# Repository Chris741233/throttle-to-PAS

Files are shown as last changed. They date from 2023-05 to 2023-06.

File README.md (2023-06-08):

# e-bike throttle to PAS converter
Arduino e-bike throttle to PAS simulation and replication \
Using a throttle (thumb throttle or accelerator) to simulate pedaling on an e-bike

Utilisation d'un throttle (gachette de pouce ou accélérateur) pour simuler un pédalage sur un e-bike.
  
Code pour Aduino Nano/Uno (signal +5V)

**see also** 
- [Button to PAS (with cruise in option)](https://github.com/Chris741233/button-to-PAS)
- [PAS to throttle converter](https://github.com/Chris741233/PAS_to_throttle)
- [PAS analyzer](https://github.com/Chris741233/PAS_analyzer)

**Discussion sur le forum Cyclurba**  
[Cyclurba](https://cyclurba.fr/forum/forum_discussion.php?from=11&discussionID=31032&messageID=741856&rubriqueID=87)  
[video de Peter (Youtube)](https://www.youtube.com/watch?v=A_oQwdZdAz4&t=2s)

---

#### Wiring (Arduino Uno/Nano)
<p align="left">
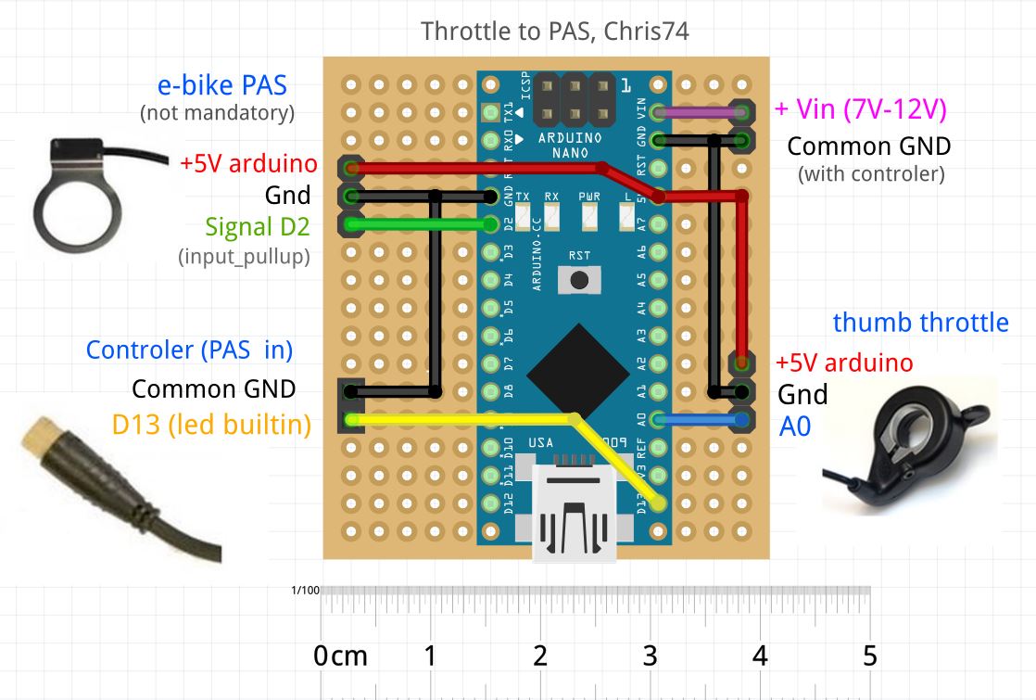
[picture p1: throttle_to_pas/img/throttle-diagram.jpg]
  
</p>

<p align="left">
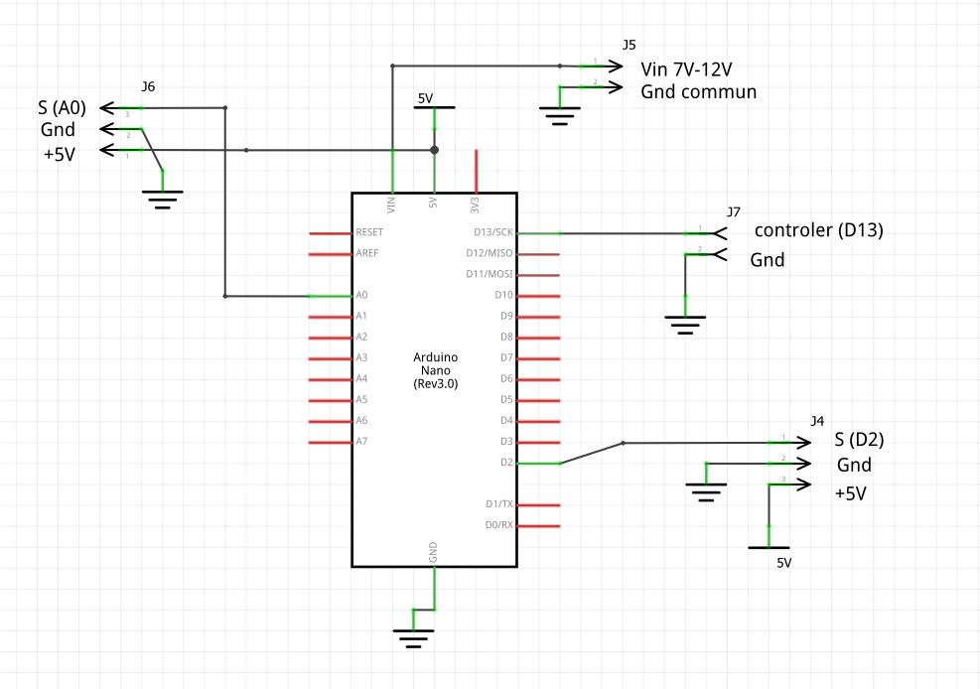
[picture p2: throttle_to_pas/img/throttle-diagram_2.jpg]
  
</p>

---

#### Utilisation
Régler les constantes en début de code \
*Adjust constants at the beginning of code*

- Calibrer les  min et max throttle en décommentant la ligne *"debug Serial"* dans le loop (le recommenter après)
- Ajuster le marge de déclenchement *"tr_margin"*
- Choisir le nb. d'aimants *"nb_magnets"* sur votre disque de PAS 
- Choisir les RPM min et et max de simulation de pédalage (valable seulement si le controleur accèpte un PAS proportionel)
- Adapter le duty-cycle high *"duty_cycle"* selon votre modèle de PAS (A ou B, voir plus bas)
- That's all :-)

```
-- Setting ---

const int   tr_min    = 220;    // throttle min  (see debug serial) 
const int   tr_max    = 856;    // throttle max  (see debug serial) 
const int tr_margin   = 15;     // margin before send PAS signal (+ tr_min and - tr_max ) 

const int   nb_magnets  = 6;    // nb. of magnets to simul (default 6p)
const int   slow_rpm  = 20;     // simul RPM pedaling min (default 20 rpm)
const int   fast_rpm  = 60;     // simul RPM pedaling max,(default 60 rpm)

const float duty_cycle = 56.70; // % duty-cycle (high signal, % period)
```
---

#### Debug val throttle min-max
<p align="left">
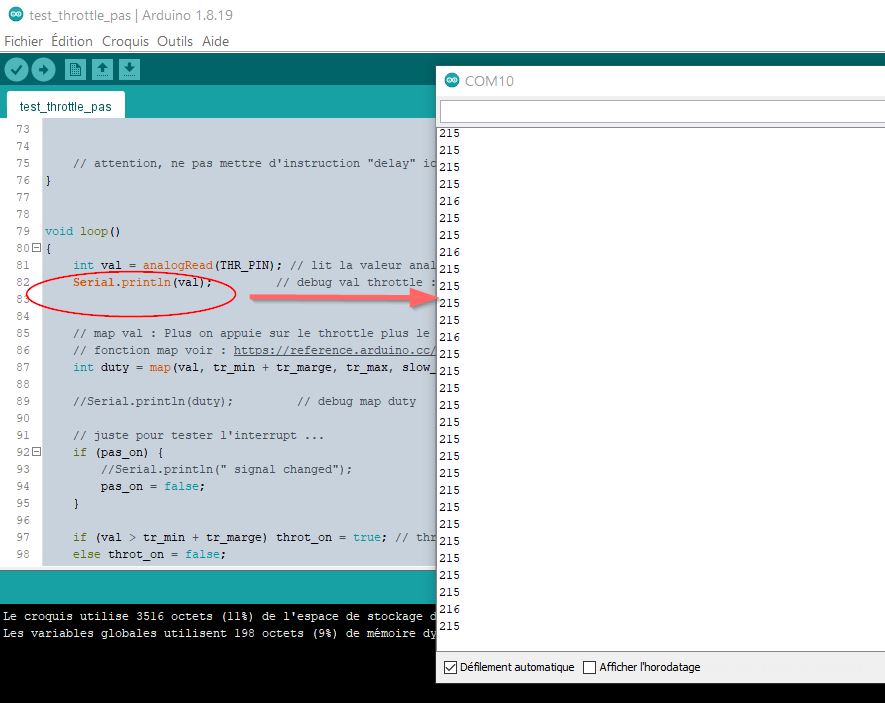
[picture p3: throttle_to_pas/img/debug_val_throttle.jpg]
serial debug
  
</p>

#### test Oscillo
<p align="left">
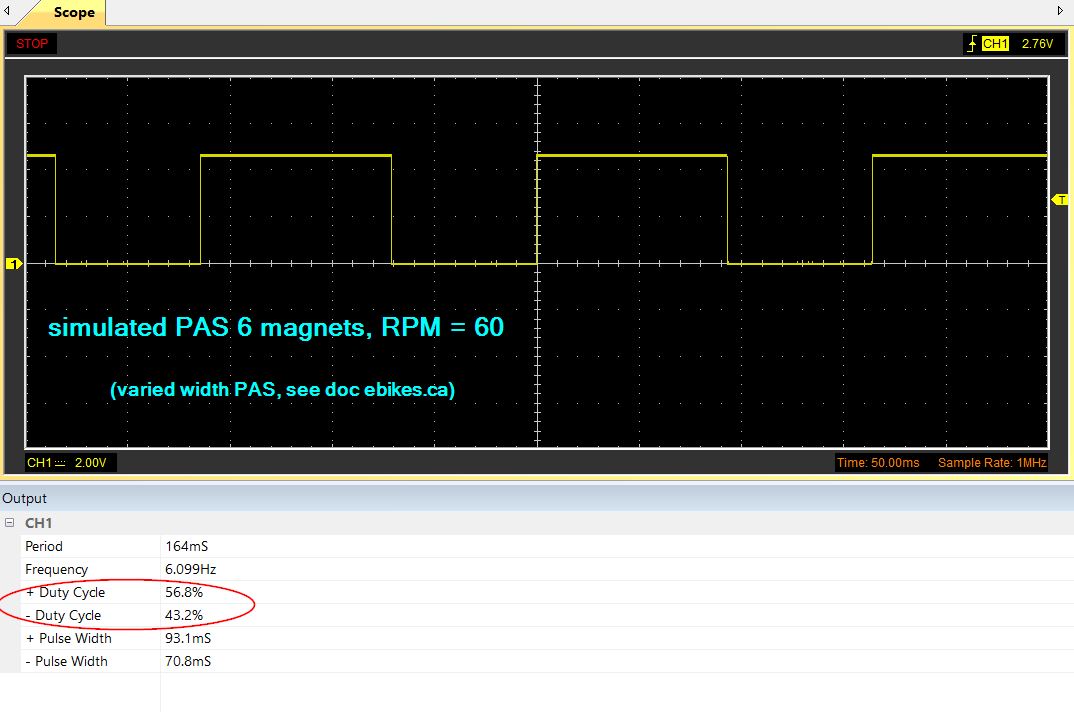
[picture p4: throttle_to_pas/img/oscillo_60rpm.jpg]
Oscillo
  
</p>

#### PAS testing
<p align="left">
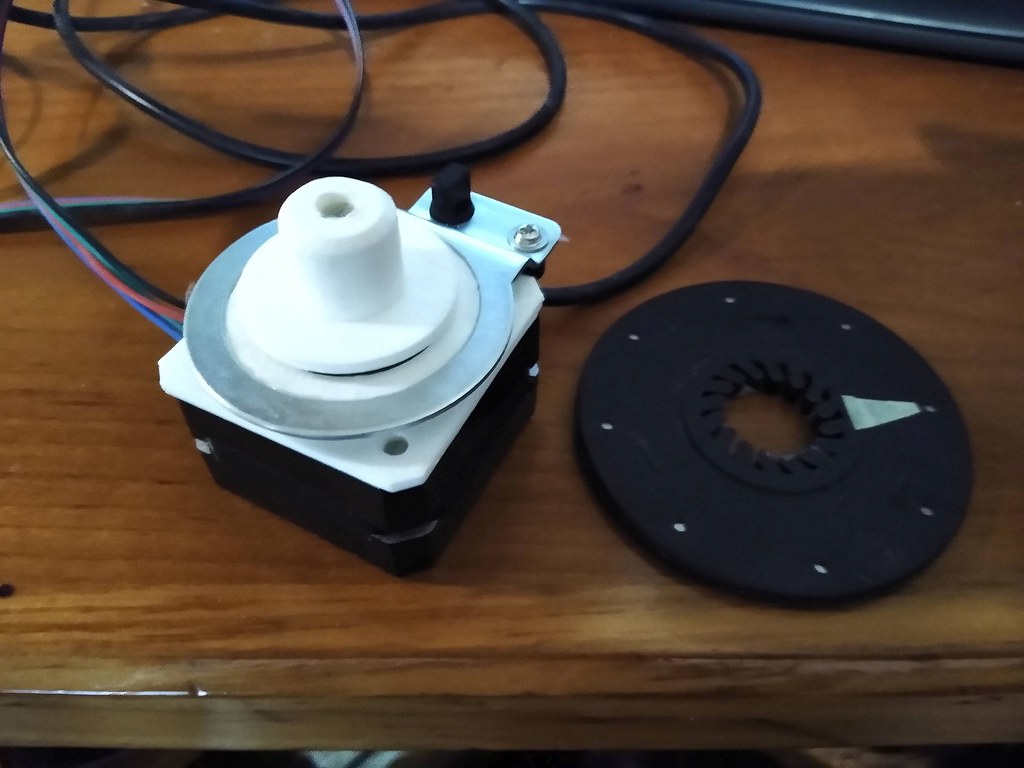
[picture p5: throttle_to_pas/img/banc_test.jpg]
PAS testing
  
</p>

#### Doc on ebikes.ca : 
[Signal Types for Basic PAS Sensors](https://ebikes.ca/learn/pedal-assist.html)

<p align="left">
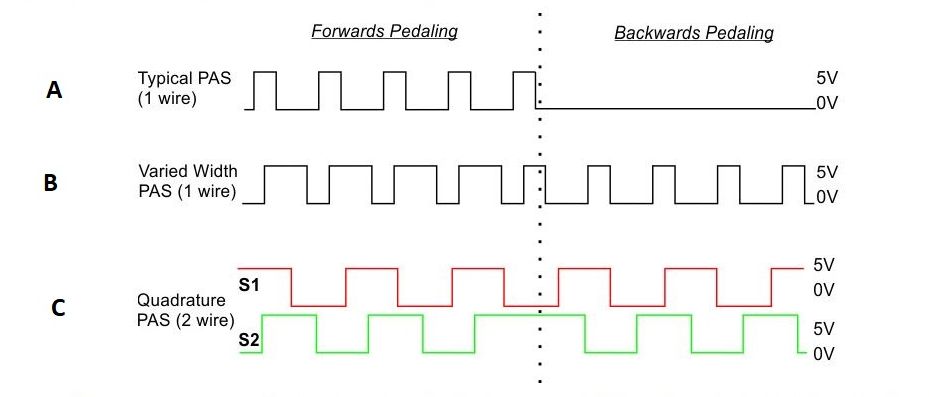
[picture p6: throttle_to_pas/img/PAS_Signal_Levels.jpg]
  
</p>

--- 
#### Note
  
> *La réglementation de certains pays n'autorise pas l'utilisation d'un accélérateur à plus de 6 km/h sans pédaler.*
*L'utilisation de ce code et schéma sont sous votre propre responsabilité !* 

> *The regulations of some countries do not allow the use of an accelerator at more than 6 km/h without pedaling.*
*The use of this code and diagram is under your own responsibility!*

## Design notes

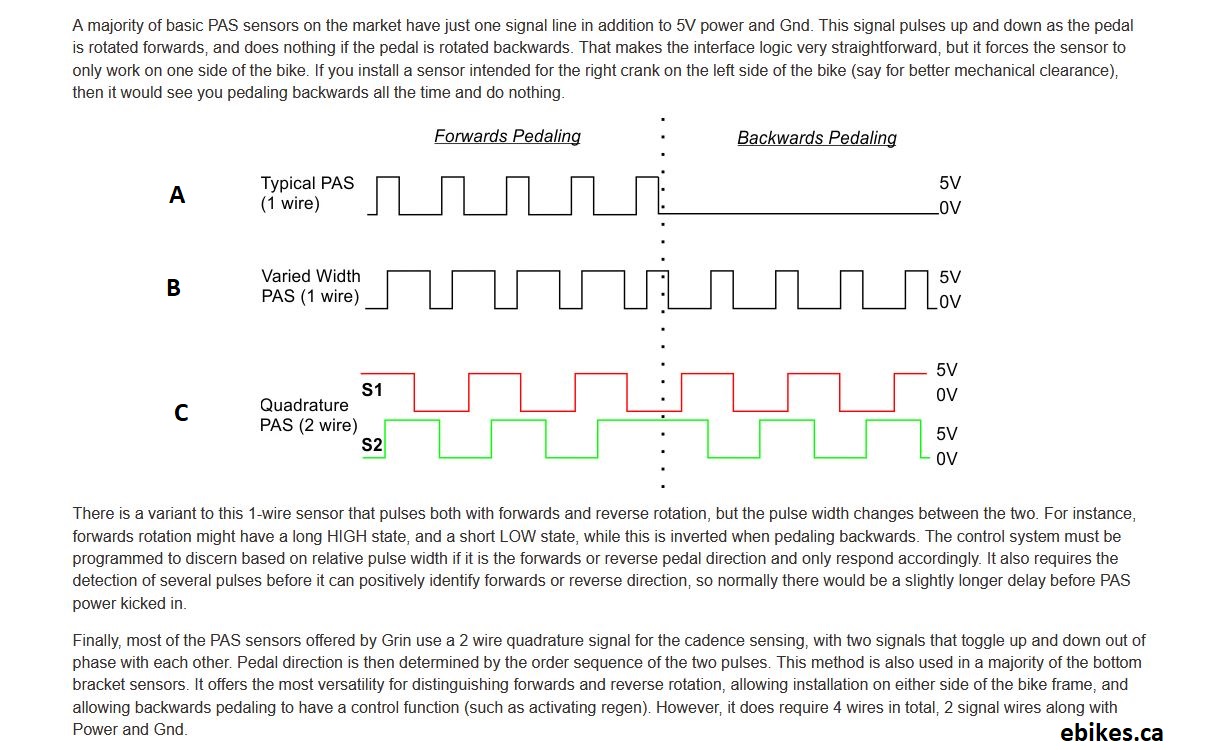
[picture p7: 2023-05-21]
throttle_to_pas/img/PAS_Signal_Levels2.jpg

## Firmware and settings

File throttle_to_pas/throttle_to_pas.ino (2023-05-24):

/******************************************************************
Created with PROGRAMINO IDE for Arduino - 17.05.2023 | 10:21:23
Project     :
Libraries   :
Author      :  Chris74

Description :  e-bike throttle to PAS - Arduino Uno/Nano
- Simulation pedalage et envoi au controleur

Code and info on Github : https://github.com/Chris741233/throttle-to-PAS


Doc PAS ebikes.ca (Signal Types for Basic PAS Sensors) : 
- https://ebikes.ca/learn/pedal-assist.html
Doc PAS on pedelecforum.de
- https://www.pedelecforum.de/forum/index.php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


Discussion Cyclurba (Soupaloignon) : 
- https://cyclurba.fr/forum/741850/arduino-l-assistance-d-un-vae.html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
- https://cyclurba.fr/forum/738995/fonctionnent-capteurs-pn-dalage.html?discussionID=5512

Other source : Pedelecs forum 
- https://www.pedelecs.co.uk/forum/threads/how-to-add-a-throttle-to-a-carrera-vengeance-e-spec.31483/


******************************************************************/



// -------- GPIO Arduino Uno/Nano --------------

const int THR_PIN = 0;   // -- THROTTLE A0

const int PAS_PIN = 2;   // -- PAS Hall D2, sans resistance (cf INPUT_PULLUP) + Interrupt

const int LED_PIN = 13;  // -- LED et CONTROLER in (D13 = LED_BUILTIN)


// -------- SETTING CONSTANTS ------------------------


// -- throttle setting (cf debug Serial in loop) 
const int   tr_min    = 220;    // throttle min - marge ajoutee dans map() 
const int   tr_max    = 856;    // throttle max - marge deduite dans map()
const int tr_margin   = 15;     // marge (margin) throttle avant envois signal PWM  et en deduction de tr_max  

// -- reglages nb. d'aimants et simulation RPM pedalage
const int   nb_magnets  = 6;      // nb. d'aimants (nb. of magnets) sur le disque du PAS (default 6p)
const int   slow_rpm  = 20;     // simulation RPM pedalier min (default 20 rpm)
const int   fast_rpm  = 60;     // simulation RPM pedalier max (default 60 rpm)

// -- setting duty-cycle high signal, cf doc ebikes.ca : https://ebikes.ca/learn/pedal-assist.html 
// -- attention var float : si nombre entier ajouter au moins une decimal .0 Par exemple 60% indiquer 60.0% !!
const float duty_cycle = 56.70;  // % duty high (56.70% on my PAS, type varied width, but 57.0% (or 60.00% ?) must be Ok




// ******** Calcul constantes : ne pas modifier a partir d'ici ! ***********
// **************************************************************

// ne pas enlever les decimales aux chiffres entiers !
const int slow_pas = (1000.0 / (slow_rpm / 60.0 * nb_magnets)) * (duty_cycle/100);   // Signal PAS high lent en ms, % duty_cycle
const int fast_pas = (1000.0 / (fast_rpm / 60.0 * nb_magnets)) * (duty_cycle/100);   // Signal PAS high rapide en ms, % duty_cycle

// calc ratio low (high/low), round 2 decimale
const float t1 = duty_cycle / (100 - duty_cycle);
const float ratio_low = floor(100*t1+0.5)/100; // round decimal to 2 digit (10 for 1 digit)

// -- expl. periode PWM ; 60Rpm / 60sec = 1Rps. 1Rps / 6poles =  1sec / 6 = 0.166 ou 166ms
// -- duty cycle 56.7% de 166ms = 94ms high
// -- ratio_low = percent / (100 - percent); // en duty high 56.75%  = ~1.30


// -------- GLOBAL VARIABLES ----------------------

unsigned long start = 0;           // timer

volatile bool throt_on = false;    // throttle in use = false au boot 
volatile bool pas_on   = false;    // test interrupt PAS 


// -------- MAIN PROG ----------------------

void setup() {
    Serial.begin(115200);
    
    pinMode(LED_PIN, OUTPUT);
    pinMode(THR_PIN, INPUT);
    
    pinMode(PAS_PIN, INPUT_PULLUP);  // PAS Hall, sans ajout de résistance, signal à 1 devant aimant
    
    digitalWrite(LED_PIN, LOW);      // signal led/controleur sur Low au boot
    
    // -- Interrupt pedaling : appel "isr_pas" sur signal CHANGE  
    attachInterrupt(digitalPinToInterrupt(PAS_PIN), isr_pas, CHANGE); 
    
    
    // attention, ne pas mettre d'instruction "delay" ici (et dans le loop egalement) !
    // no delay() here !
    
}


void loop()
{
    int val = analogRead(THR_PIN); // lit la valeur analogique du throttle 
    //Serial.println(val);         // debug val throttle : env. 210 au min et 860 au max sur mon montage
    
    
    // map val : Plus on appuie sur le throttle plus le signal PAS high doit etre court !
    int duty = map(val, tr_min+tr_margin, tr_max-tr_margin, slow_pas, fast_pas);
    
    //Serial.println(duty);             // debug duty
    //Serial.println(t1, 5);            // debug ratio
    //Serial.println(ratio_low, 5);     // debug ratio
    
    // juste pour tester l'interrupt ...
    if (pas_on) {
        //Serial.println(" signal changed");
        pas_on = false;
    }
    
    // si throttle en fonction on simule un signal PAS, fréquence et duty selon throttle
    if (val > tr_min + tr_margin) {
        
        throt_on = true; 
        
        // Signal high
        start = millis();
        while (millis() - start <= duty) {
            if (val > tr_min + tr_margin) digitalWrite(LED_PIN, HIGH);
        }
        // Signal low ( ratio calcule dans constantes)
        start = millis();
        while (millis() - start <= duty / ratio_low) {
            if (val > tr_min + tr_margin) digitalWrite(LED_PIN, LOW);
        }
    }
    else throt_on = false;
    
    
    // No delay() here !
    
} // end loop


// -- ISR - appel interrupt 
// - simple replication des signaux du PAS vers le controleur lors du mode pedalage sans appuyer sur le throttle
void isr_pas() {
    
    pas_on = true;    
    
    // replication du pedalge seulement si le throttle n'est pas en fonction
    if (throt_on == false) { 
        
        if (digitalRead(PAS_PIN) == HIGH) digitalWrite(LED_PIN, HIGH);
        else  digitalWrite(LED_PIN, LOW);
        //Serial.println("pedalage..."); // pour debug, eviter si possible un serial dans une interruption
    } 
    
} // endfunc
